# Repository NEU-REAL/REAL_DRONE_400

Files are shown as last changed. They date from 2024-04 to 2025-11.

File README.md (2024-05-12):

# **【东北大学REAL实验室】自主无人机组装教程** 

Github链接 [REAL_DRONE_400](https://github.com/NEU-REAL/REAL_DRONE_400/) An open source Drone Suite for Aerial Robot.

本文档是视频教程[【东北大学REAL实验室】自主无人机组装教学视频](https://www.bilibili.com/video/BV1hC411H7rh/)的配套文档

实验室主页 [东北大学REAL-LAB 环境感知与自主导航实验室](http://faculty.neu.edu.cn/fangzheng/zh_CN/zdylm/262140/list/index.htm)

  <div align=center>
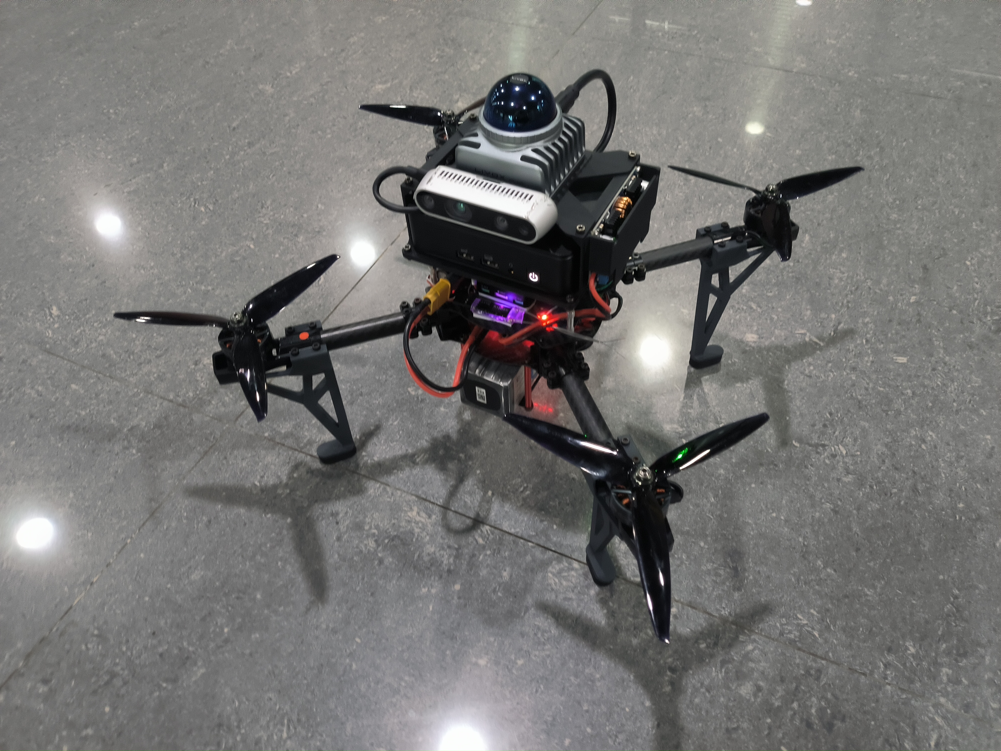
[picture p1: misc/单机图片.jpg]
  
  </div>

⭐项目亮点⭐

⭐结构件 动力套开源

⭐免雷达驱动一键编译

⭐输出高频雷达定位信息。

<font color="#dd0000">**教程简介**</font>

本次课程是一套面向对自主空中机器人感兴趣的学生、爱好者、相关从业人员的免费课程，包含了从硬件组装、代码部署、实机实验等全套详细流程。提供一种Fast-Drone-250的升级大负载能力、稳定定位版本自主无人机。本次课程所涉及的所有代码、硬件设计全部开源。<font color="#dd0000">严禁商用与转载，版权与最终解释权由东北大学REAL实验室所有。</font>

<font color="#dd0000">**安全事项**</font>

四旋翼无人机具有较高的安全风险，请同学们严格遵守安全规范，不要在有人的室内或室外进行试验，对自己和他人的安全负责，本实验室完全免责。

<font color="#dd0000">**致谢**</font>

感谢飞哥组里的小伙伴们提供的支持以及[FAST-DRONE-250开源项目](https://github.com/ZJU-FAST-Lab/Fast-Drone-250)以及[完整课程](https://www.shenlanxueyuan.com/course/385?source=1)。有兴趣的各位可以去点点⭐。

感谢组内指导老师方正教授的大力支持。

感谢一起调试、设计本构型无人机、提供了大力帮助的好伙伴孙哥和白哥。

# 教程视频链接：
- [第一节：无人机简介与电气连接](https://www.bilibili.com/video/BV1hC411H7rh/?vd_source=a901441d2c723973826f98ab4b1463a5)
- [第二节：工作台与焊接讲解](https://www.bilibili.com/video/BV1zC411H7ij/?vd_source=a901441d2c723973826f98ab4b1463a5)
- [第三节：无人机装配与飞控设置](https://www.bilibili.com/video/BV1Nx4y167wC/?vd_source=a901441d2c723973826f98ab4b1463a5)
- [第四节：PX4_Ctrl FSM讲解与真机定点飞行](https://www.bilibili.com/video/BV11i421y7ta/?vd_source=a901441d2c723973826f98ab4b1463a5)
- [第五节：Preception & Planning与真机飞行](https://www.bilibili.com/video/BV1G1421X7sd/?vd_source=a901441d2c723973826f98ab4b1463a5)

# 项目文件说明：
  项目中分为几个文件夹：
- [files](/files/) 文件夹用于存放各类相关文件
- [home_shfiles](/home_shfiles/) 存放了快速启动脚本，请将此目录下的脚本放置于home路径下以快速启动
- [misc](/misc/) 文件夹存放项目相关的图片资料
- [release](/release/) 文件夹存放项目的硬件设计资料，其中[3MF](/release/3MF/)文件夹存放需要打印的部件模型，我们使用拓竹X1C打印机进行3D打印部分材料制作，耗材使用拓竹PLA-CF。[PRODUCTION](/release/PRODUCTION/)文件夹存放可以直接打印的切片工程。[STEP](/release/STEP/)文件夹存放项目相关的所有硬件设计素材，以STEP文件给出。
- [src](/src/) 文件夹放置项目源码文件。

## 第一章：无人机简介与电气连接
  本次课程与高飞老师的[从零制作自主空中机器人](https://www.bilibili.com/video/BV1WZ4y167me?p=1)同样是一套面向对自主空中机器人感兴趣的学生、爱好者、相关从业人员的免费课程，包含了从硬件组装、机载电脑环境设置、代码部署、实机实验等全套详细流程，带你从0开始，组装属于自己的自主无人机，并让它可以在未知的环境中自由避障穿行。本次课程所涉及的所有代码、硬件设计全部开源，<font color="#dd0000">严禁商用与转载，版权与最终解释权由东北大学REAL实验室所有。</font>

  本次课程的重心主要落在自主空中机器人的搭建、代码部署及调试上，关于自主空中机器人的一些理论基础，例如动力学模型，路径搜索，轨迹规划，地图构建等内容，高飞老师在深蓝学院有非常详尽而深入浅出的[课程](https://www.shenlanxueyuan.com/course/385?source=1)，本次课程就不再赘述。

## 第二章：动力套焊接
  机器人本体相关配件及焊接用工具详见[purchase_list.xlsx](files/purchase_list.xlsx)

  **特别强调，四合一电调的输入电源线需要并联配套电解电容，且输入电源线规格至少应在14AWG以上，推荐12AWG与电池一致，保证过流能力！**

  焊接目标如图
  <div align=center>
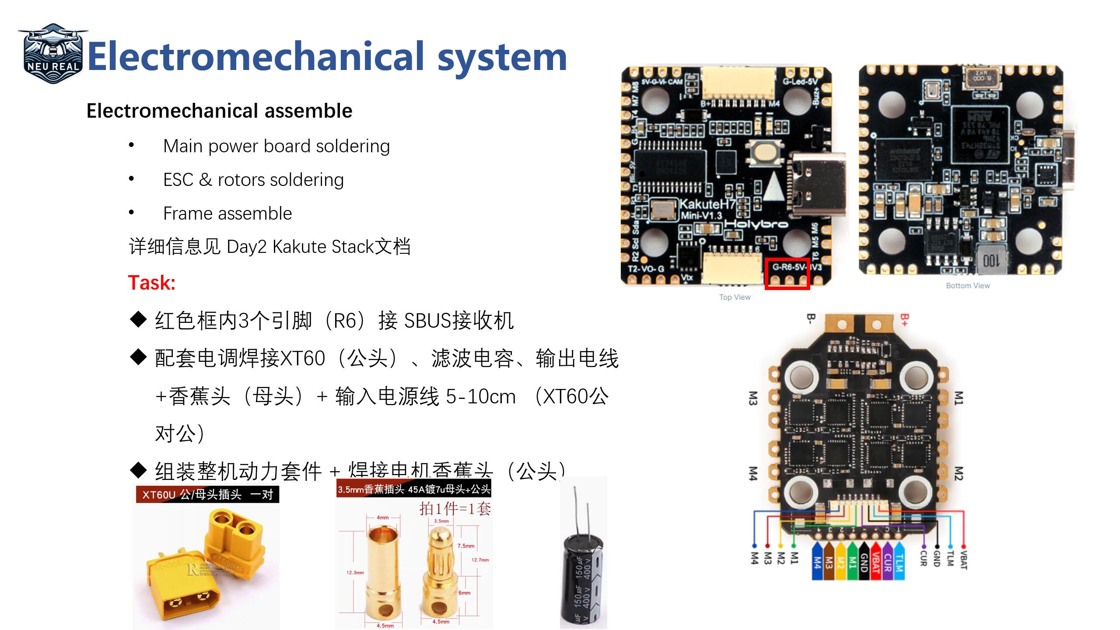
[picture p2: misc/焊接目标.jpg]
  
  </div>

  焊接最终结果如图
  <div align=center>
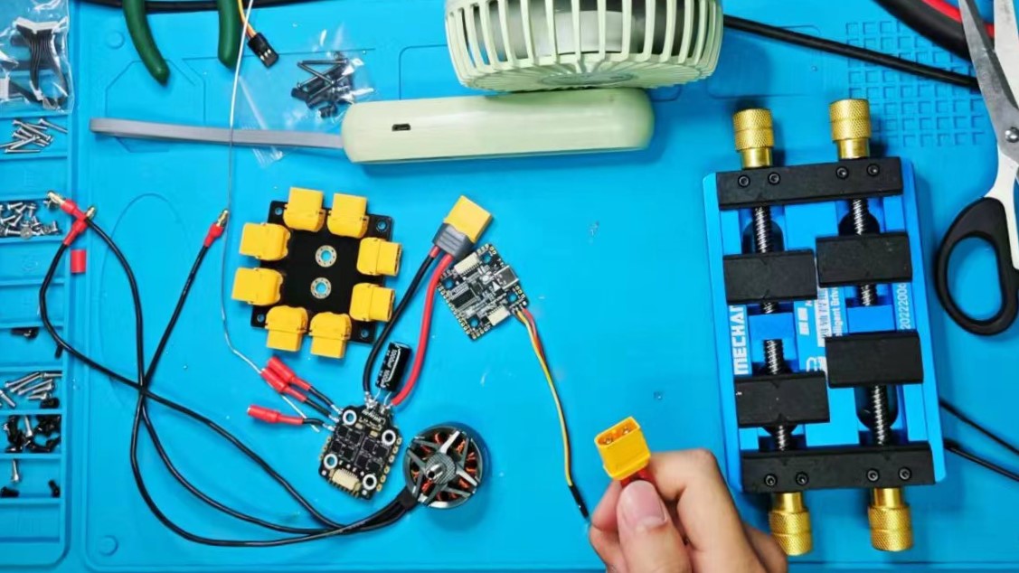
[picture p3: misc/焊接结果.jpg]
  
  </div>

## 第三章：无人机装配与飞控设置

使用QGC连接飞控，如果无法识别为PX4飞控，例如下图：
  <div align=center>
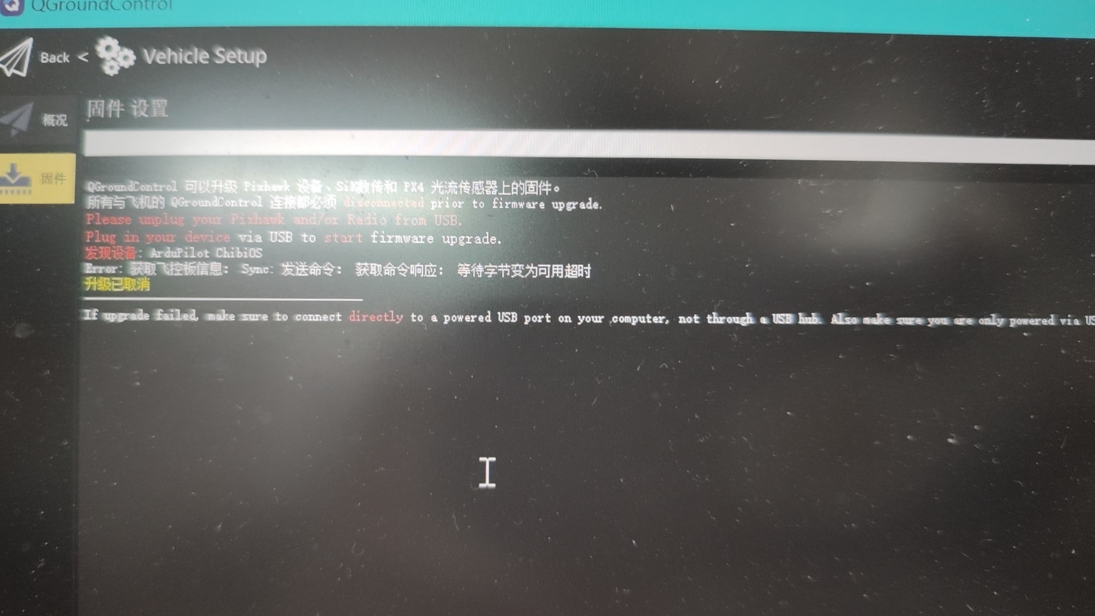
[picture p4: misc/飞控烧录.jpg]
  
  </div>

请按照以下步骤使用dfu-util 工具在ubuntu下刷飞控bootloader：

1.	长按飞控按钮同时插typec连接电脑，按里面txt的命令，在ubuntu下刷引导进去，注意路径
dfu-util -a 0 --dfuse-address 0x08000000 -D ./holybro_kakuteh7mini_bootloader/holybro_kakuteh7mini_bootloader.bin  

2.	进入qgc的固件界面，再重新插拔，自定义安装压缩包里的px4
再重新插拔应该就有了，这个操作可能会报error，不用管他。

    注意：刷1.14 beta版 
    stable版有bug会导致炸机 Dshot不是很稳定会导致怠速过快
    推荐用PWM400输出电调并调整死区至怠速解锁

* 上电前请先用万用表通断档检测电源正负焊点是否短接，强烈建议第一次上电前先接一个[短路保护器](https://item.taobao.com/item.htm?spm=a230r.1.14.6.72b83b20uNbZk7&id=656973651729&ns=1&abbucket=19#detail)

* <font color="#dd0000">检测电机转向前确保没有安装螺旋桨！！！！</font>

* 修改电机转向：调整转向错误电机的3根连接线中的其中两根交换相接即可。

## 第四章：PX4_Ctrl FSM讲解与真机定点飞行
- 自动起飞与定点控制
```
sh start_sensor.sh；
sh start_mapping.sh；
rostopic echo /Odom_high_freq；
```
拿起飞机进行缓慢的小范围晃动，放回原地后确认没有太大误差；
遥控器5通道拨到内侧，6通道拨到下侧，油门打到中位；
```
sh start_run_ctrl.sh；
sh start_takeoff.sh;
```
如果飞机螺旋桨开始旋转，但无法起飞，说明hover_percent参数过小；如果飞机有明显飞过1米高，再下降的样子，说明hover_percent参数过大；
遥控器此时可以以类似大疆飞机的操作逻辑对无人机进行位置控制；
```
sh start_land.sh
```
降落时把油门打到最低，等无人机降到地上后，把5通道拨到中间，左手杆打到左下角上锁。

## 第五章：Preception & Planning与真机飞行
  确认图中参数：
  <div align=center>
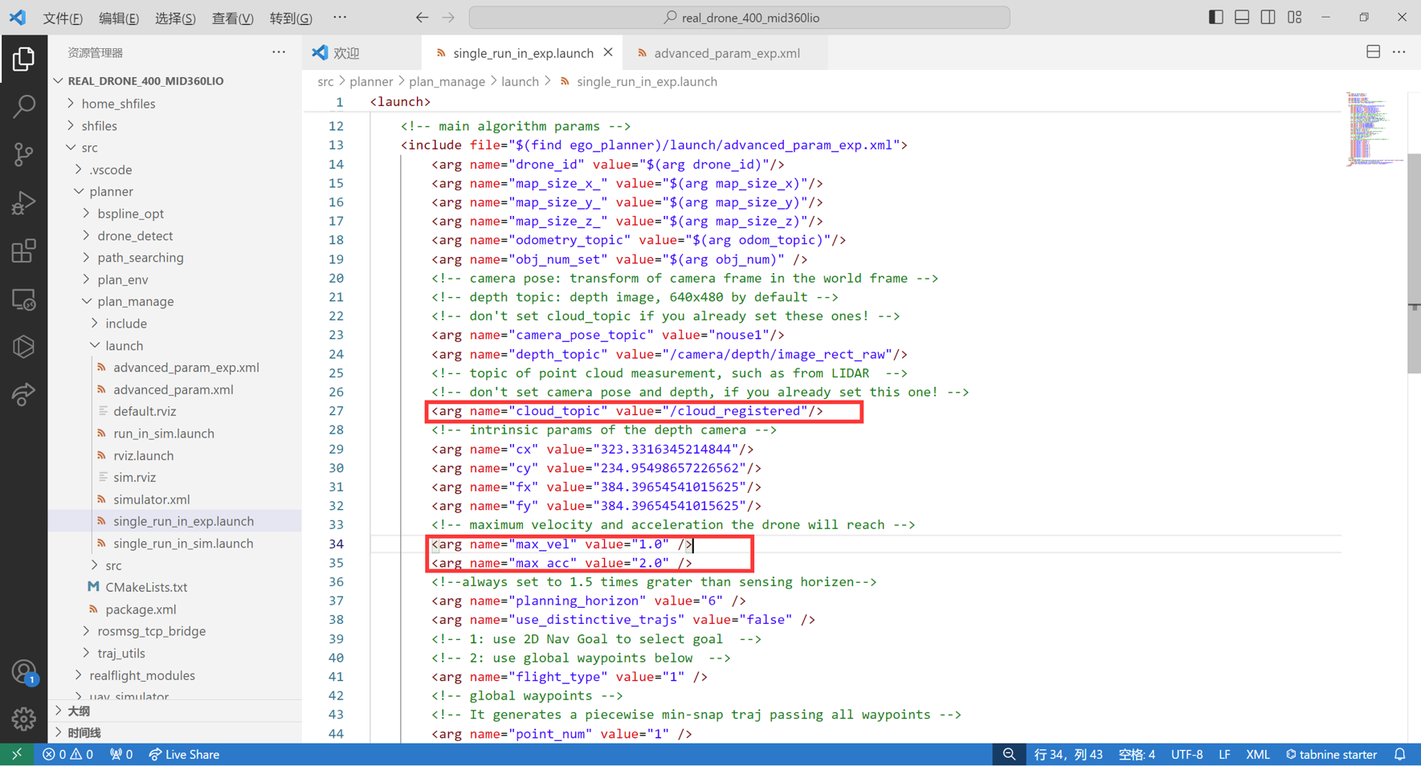
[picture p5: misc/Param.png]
  
  </div>

- Ego-Planner 真机测试

1.启动传感器与定位
```
sh start_sensor.sh；
sh start_mapping.sh；
rostopic echo /Odom_high_freq；
```
2.启动Ego-Planner与Rviz
```
sh start_planner.sh;
sh start_rviz.sh;
```
3.启动PX4_ctrl后确认摇杆正确，自动起飞
```
sh start_run_ctrl.sh；
sh start_takeoff.sh;
```
按下G键加鼠标左键点选目标点使无人机飞行。

4.任务完成后使用自动降落
```
sh start_land.sh；
```

# 合作与维护
我们会努力扩展所提出的系统并提高代码可靠性。持续维护这个项目

如有任何技术问题，请使用此项目的ISSUE功能。

如有商业咨询，请联系东北大学 方正 教授 (fangzheng@mail.neu.edu.cn)。

# 补充说明：
  如果你觉得这个项目对你能够有所帮助，可以点点⭐或者转发分享哦。
  
  附带几组3D设计图与实物图的对照：
  
  1.整机比对
  <div align=center>
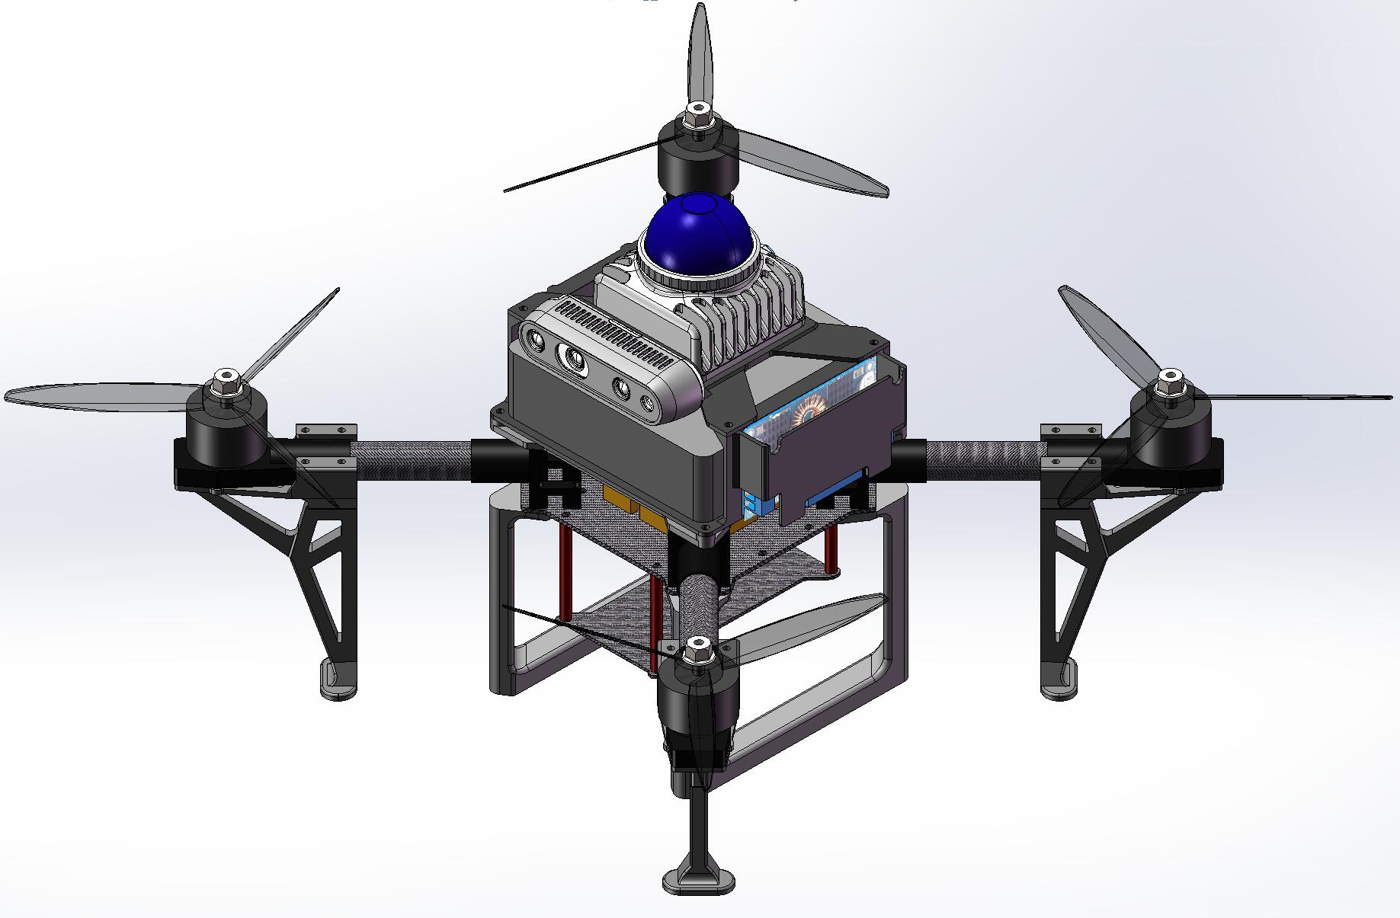
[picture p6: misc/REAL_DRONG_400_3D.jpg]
  
  </div>
  2.动力套件
  <div align=center>
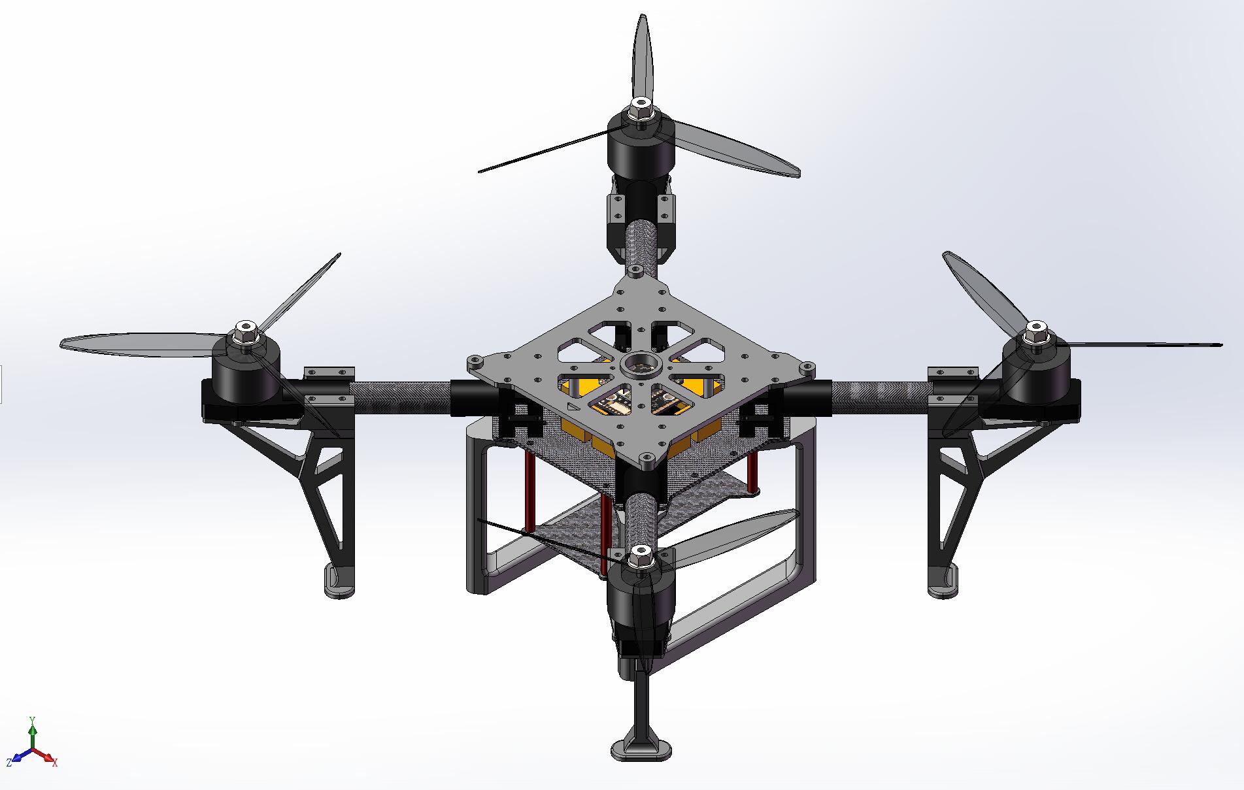
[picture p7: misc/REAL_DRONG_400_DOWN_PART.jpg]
  
  </div>
  3.感知模块
  <div align=center>
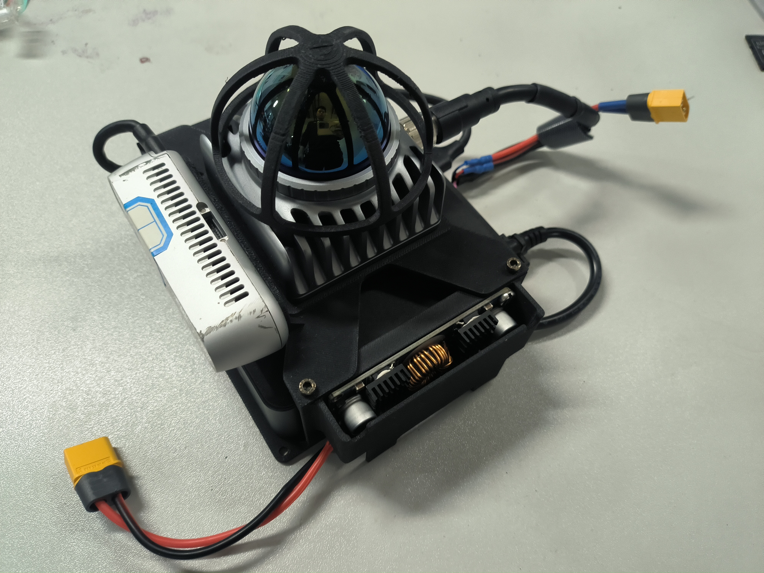
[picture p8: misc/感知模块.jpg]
  
  </div>

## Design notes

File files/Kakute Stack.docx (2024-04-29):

Kakute Mini H7 烧录教程 v1.1

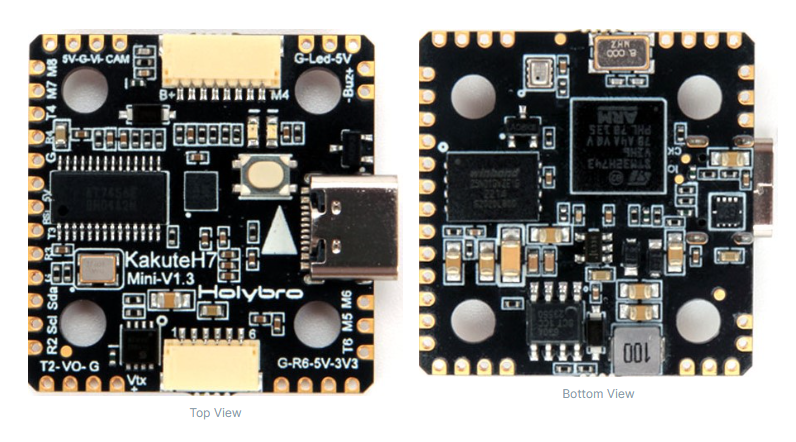
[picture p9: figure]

红色框内3个引脚（R6）接 SBUS接收机

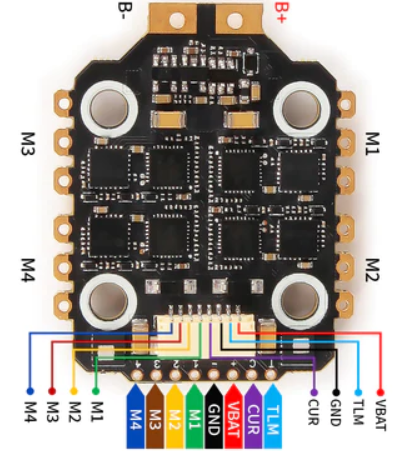
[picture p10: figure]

配套电调

1. 长按飞控按钮同时插typec连接电脑，按里面txt的命令，在ubuntu下刷引导进去，注意路径

dfu-util -a 0 --dfuse-address 0x08000000 -D ./holybro_kakuteh7mini_bootloader/holybro_kakuteh7mini_bootloader.bin

2. 进入qgc的固件界面，再重新插拔，自定义安装压缩包里的px4

再重新插拔应该就有了，这个操作可能会报error，不用管他。

注意：刷1.14 beta版

stable版有bug会导致炸机 Dshot不是很稳定会导致怠速过快

推荐用PWM400输出电调并调整死区至怠速解锁

PX4安装上就ok了，重新插拔可能会很慢连上，实在连不上就换Windows的qgc或者更新qgc试试

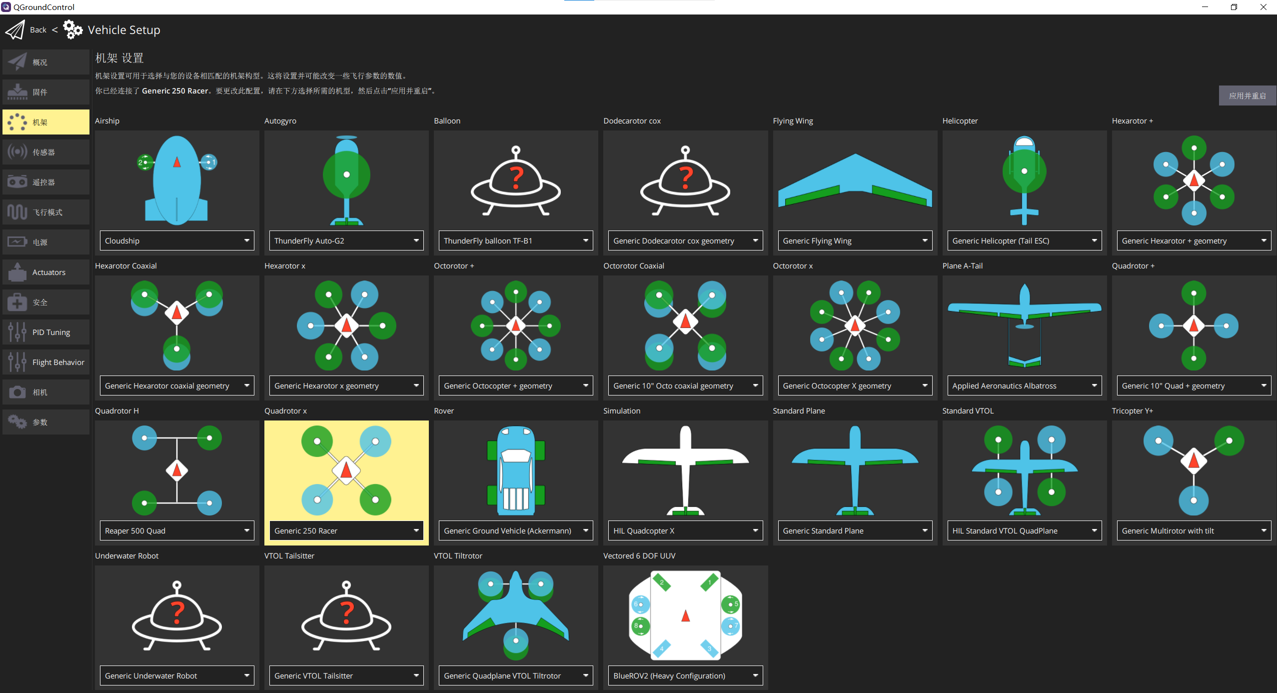
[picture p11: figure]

机架选择

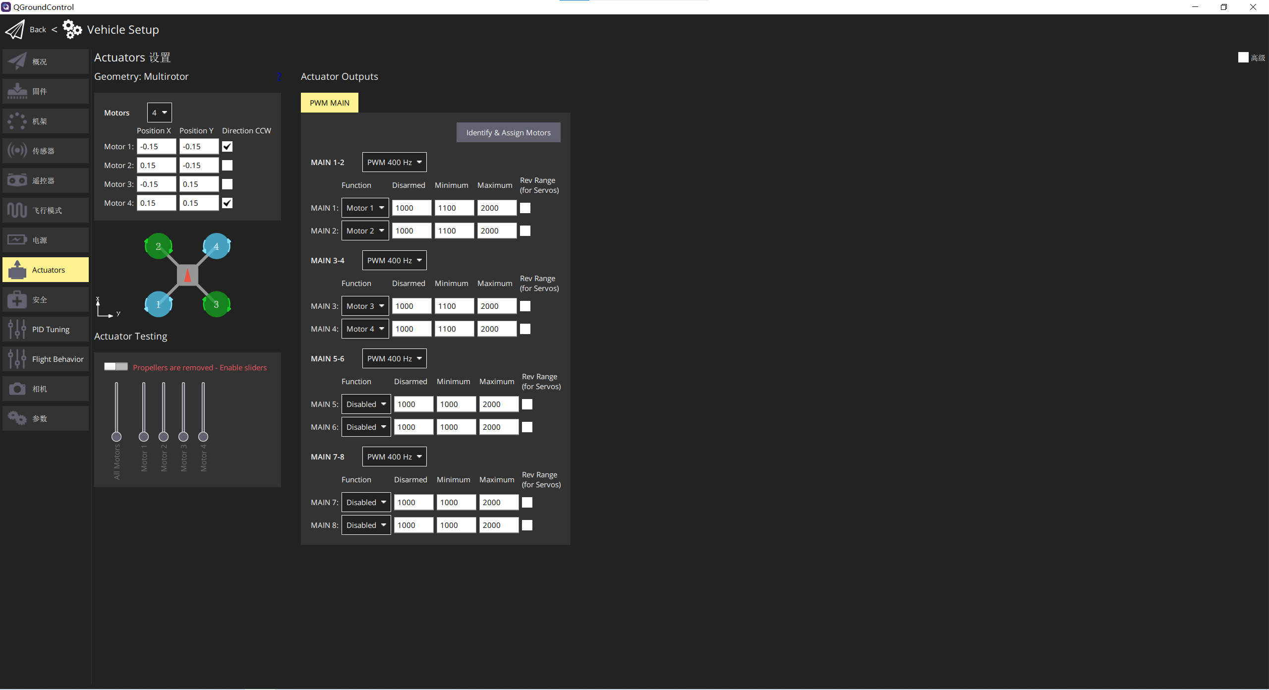
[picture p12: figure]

机架电机设置

©相关文档链接：

Kakute H7 Mini – Holybro Store (https://holybro.com/products/kakute-h7-mini)

Kakute H7 Mini Stacks – Holybro Store (https://holybro.com/products/kakute-h7-mini-stacks?variant=42940542746813)

Tekko32 F4 4in1 Mini 50A ESC – Holybro Store (https://holybro.com/products/tekko32-f4-4in1-mini-50a-esc?_pos=2&_psq=tekko32&_ss=e&_v=1.0)

Overview - Holybro Docs (https://docs.holybro.com/autopilot/kakute-h7-v1-v2-mini/kakute-h7-mini/overview)

Holybro Kakute H7 mini | PX4 自动驾驶用户指南 (main) (https://docs.px4.io/main/zh/flight_controller/kakuteh7mini.html)

PX4 Bootloader Flashing onto Betaflight Systems | PX4 自动驾驶用户指南 (main) (https://docs.px4.io/main/zh/advanced_config/bootloader_update_from_betaflight.html)

Update 2023.12.10 By Kangkang

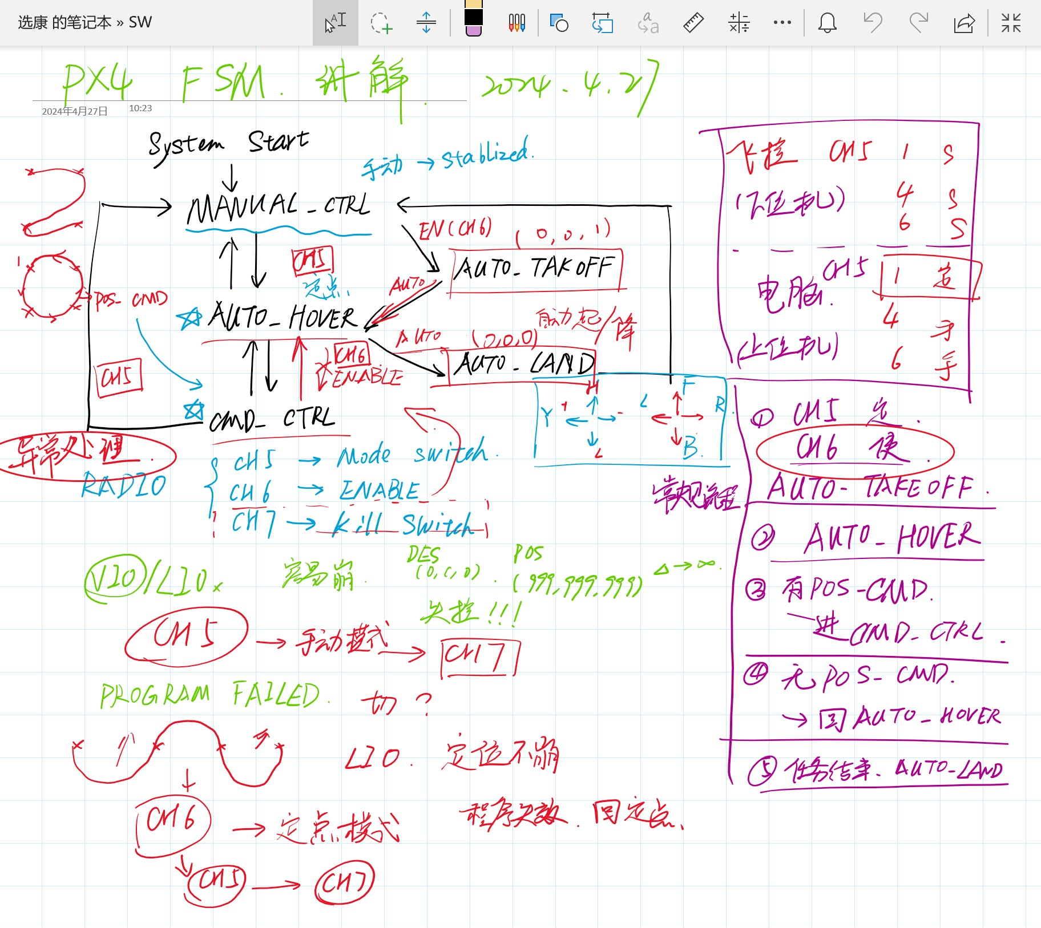
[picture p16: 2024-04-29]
misc/Handwriting.png

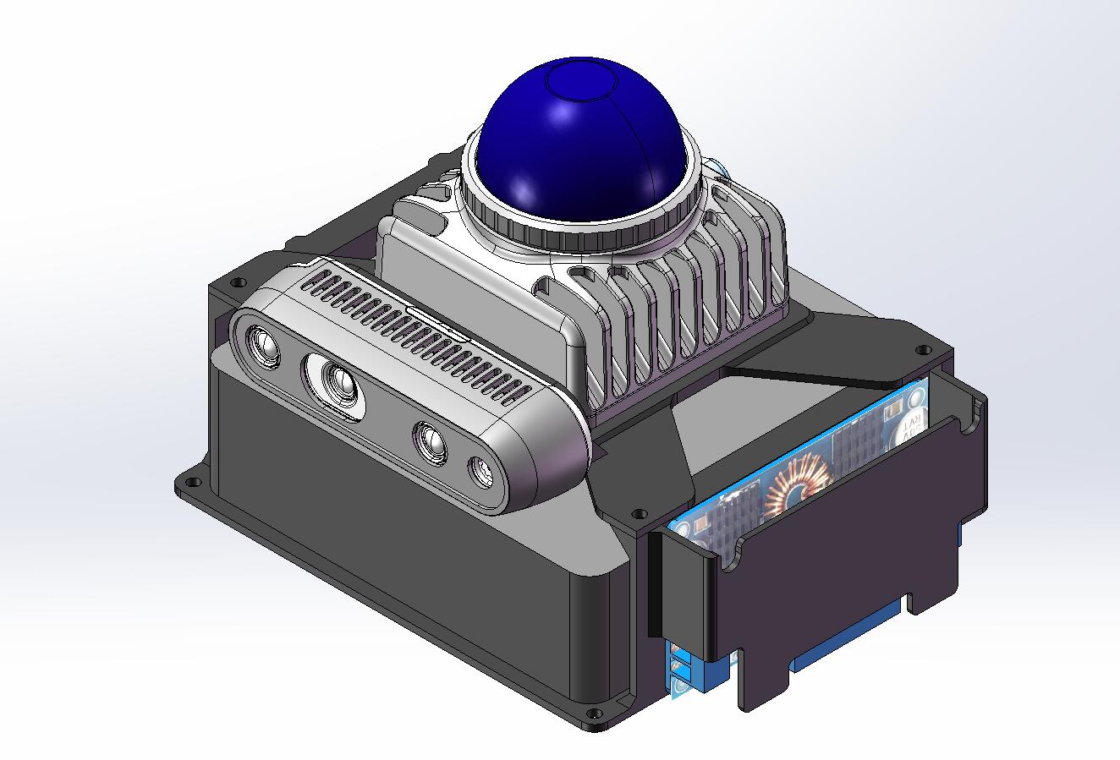
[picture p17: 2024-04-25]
misc/REAL_DRONG_400_UPPER_PART.jpg

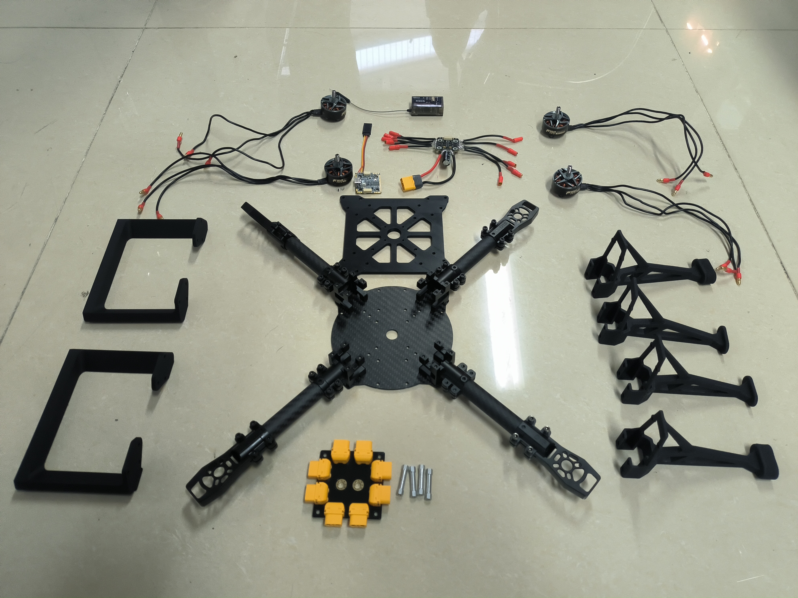
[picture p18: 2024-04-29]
misc/零件图.jpg

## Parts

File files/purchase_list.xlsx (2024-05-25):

类目 | 型号 | 数量 | 单价 | 总价 | 购买链接
动力套装
机架 | LJI-X400 Pro | 1 | 288 | 288 | https://item.taobao.com/item.htm?_u=d3ovgp2s356d&id=661322510447&sku_properties=31309:16741168228
无刷电机 | T-Motor F100 KV1100 | 4 | 229 | 916 | https://item.taobao.com/item.htm?_u=d3ovgp2s37a9&id=666218265469&sku_properties=31309:18046510136
飞控+电调 | H7 MINI + F4 4IN1 MINI 50A ESC | 1 | 916 | 916 | https://item.taobao.com/item.htm?_u=d3ovgp2s075e&id=695089334583&skuId=4934678877288
桨叶 | HQ 7040-3 | 1 | 15 | 15 | https://item.taobao.com/item.htm?_u=t3ovgp2s460a&id=671633881954&skuId=5010241515719
接收机 | 乐迪 R12DSM | 1 | 93 | 93 | https://item.taobao.com/item.htm?spm=a1z09.2.0.0.2abd2e8da0sHzh&id=541658831753&_u=l32egecq5116
遥控器 | 乐迪 AT9S PRO 左手不回中 | 1 | 545 | 545 | https://item.taobao.com/item.htm?_u=t3ovgp2s8571&id=620560690486&skuId=4648673175694
电池 | 格氏 4000mAh 6S | 1 | 488 | 488 | https://detail.tmall.com/item.htm?_u=t3ovgp2sa7dc&id=14832015119&spm=a1z09.2.0.0.32aa2e8df64WUL
穿越机脚垫 | 30*15*10mm | 1 | 16.99 | 16.99 | https://item.taobao.com/item.htm?_u=t3ovgp2se7b0&id=562158533089&skuId=3961675618573
 |  |  | 动力套成本 | 3277.99
感知模块配件
DC供电线 | XT60 | 1 | 13 | 13 | https://item.taobao.com/item.htm?spm=a1z09.2.0.0.773d2e8despLGo&id=613472402389&_u=g2epqo5e38f7
飞控连接线 | 双左弯0.15m | 1 | 9.5 | 9.5 | https://detail.tmall.com/item.htm?id=43144333772&_u=i32egecqf5d3&skuId=4498792030458
TYPEC连接线 | 15cm | 1 | 22.9 | 22.9 | https://detail.tmall.com/item.htm?id=617461584216&spm=a1z09.2.0.0.2abd2e8da0sHzh&_u=l32egecq0e19
HDMI欺骗器 |  | 1 | 3 | 3 | https://item.taobao.com/item.htm?id=600829968368&ali_trackid=1_b8192277632fc8796a134ac616741b67
DC-DC稳压模块 | LTC3780 | 1 | 38 | 38 | https://item.taobao.com/item.htm?_u=p3ovgp2s988d&id=537511849240&spm=a1z09.2.0.0.19c62e8dwykGML
 |  |  | 感知模块配件成本 | 48.4
感知模块核心
机载电脑 | Intel NUC 猛虎峡谷 准系统 i5 薄款 | 1 | 2590 | 2590 | https://item.taobao.com/item.htm?id=638758423001&ns=1&abbucket=3
 | 三星 DDR4内存条 8G 3200hz | 1 | 229 | 229 | https://detail.tmall.com/item.htm?id=541378489978&spm=a1z09.2.0.0.ea4d2e8dwctqDn&_u=t2epqo5eaa9f
 | 影驰黑将 250G M.2固态硬盘 | 1 | 234 | 234 | https://detail.tmall.com/item.htm?id=541378489978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
双目深度相机 | INTEL REALSENSE D435 | 1 | 2180 | 2180 | https://item.taobao.com/item.htm?spm=a1z10.1-c.w4004-8474743471.36.1f164e1fL0mvDM&id=670494420704
激光雷达 | Livox Mid-360 | 1 | 3999 | 3999 | https://store.dji.com/cn/product/livox-mid-360?vid=130851
 |  |  | 感知模块核心成本 | 9232
3D打印零件
上板 | 上板 | 1 | Nan | Nan
脚架 | 脚架 | 1 | Nan | Nan
感知模块支架 | 感知模块支架 | 1 | Nan | Nan
 |  |  | 3D打印成本 | Nan
配件
硅胶线 | 20,18,16AWG | 若干 | Nan | Nan | https://item.taobao.com/item.htm?id=631990884181&ns=1&abbucket=3
BB响 |  | 1 | Nan | Nan | https://item.taobao.com/item.htm?id=13954041762&ns=1&abbucket=3
硅胶杜邦线 | 10cm,15cm，公对母 | 若干 | Nan | Nan | https://item.taobao.com/item.htm?id=567943637652&ali_trackid=1_82cb0cae98e77d6ab8f389660ffac1cf
3.5mm香蕉头 公母头 |  | 12 | Nan | Nan
XT60公、母头 |  | 1 | Nan | Nan
双通铝柱 | M3*25 | 4 | Nan | Nan | https://item.taobao.com/item.htm?id=603331087035&ns=1&abbucket=13
3M双面胶 | 20mm*3m | 1 | Nan | Nan | https://detail.tmall.com/item.htm?id=653733592411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
螺丝 | M3*6mm M3*8mm 杯头 | 若干 | Nan | Nan | https://detail.tmall.com/item.htm?id=624811454452&_u=i32egecq19dc&skuId=4601948603338
 |  |  | 配件成本 | Nan
工具
烙铁 | AT937标配 | 143 | 1 | 143 | https://item.taobao.com/item.htm?id=7800035658&ns=1&abbucket=14
烙铁头 | 900M-1.6K | 11 | 1 | 11 | https://item.taobao.com/item.htm?spm=a1z10.3-c-s.w4002-23344838098.27.754f1004qeCAY6&id=579728085148
海绵 |  | 2 | 1 | 2 | https://item.taobao.com/item.htm?spm=a1z10.3-c-s.w4002-23344838098.9.6d6c1004U43LPK&id=7586598250
焊锡 | 0.5mm 500g | 76.67 | 1 | 76.67 | https://detail.tmall.com/item.htm?spm=a230r.1.14.11.552520bejLfPiP&id=43741015860&ns=1&abbucket=14
夹持台 | 褐色 | 75 | 1 | 75 | https://item.taobao.com/item.htm?id=613902998667&ali_trackid=1_a8d9bfa88456e4bdeb5141959028dacf
扳手 |  | 11 | 1 | 11 | https://item.taobao.com/item.htm?id=610029436080&ns=1&abbucket=14
螺丝刀 | 2.0mm、2.5mm | 10.99 | 1 | 10.99 | https://detail.tmall.com/item.htm?id=572329178882&cm_id=140105335569ed55e27b&abbucket=14
万用表 |  | 49 | 1 | 49 | https://item.jd.com/100000287597.html
剪刀 | 3把中号 | 10.9 | 0.33 | 3.597 | https://item.jd.com/6020791.html
切割垫 | A3 | 19.9 | 1 | 19.9 | https://item.jd.com/100001317628.html
 |  |  | 工具成本 | 402.157

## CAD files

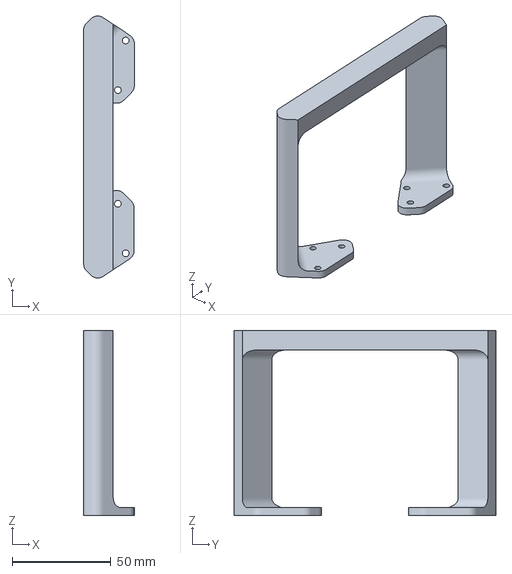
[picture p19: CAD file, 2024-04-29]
release/3MF/horrizon_land_support.3MF
25.8 x 133.0 x 94.0 mm

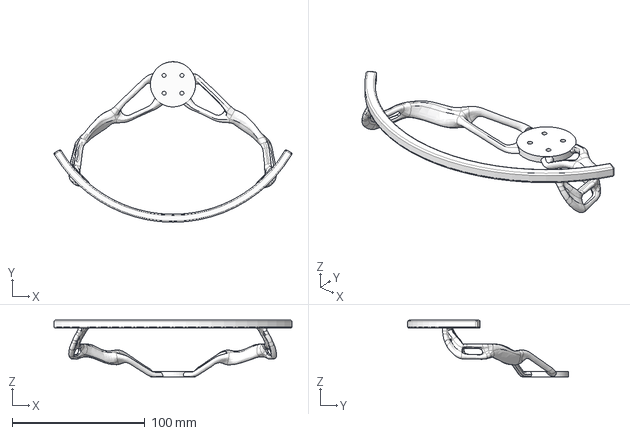
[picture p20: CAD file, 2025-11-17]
release/Derivative Design/R7040_GD_0525_001_Result_001.step
179.1 x 120.8 x 42.6 mm

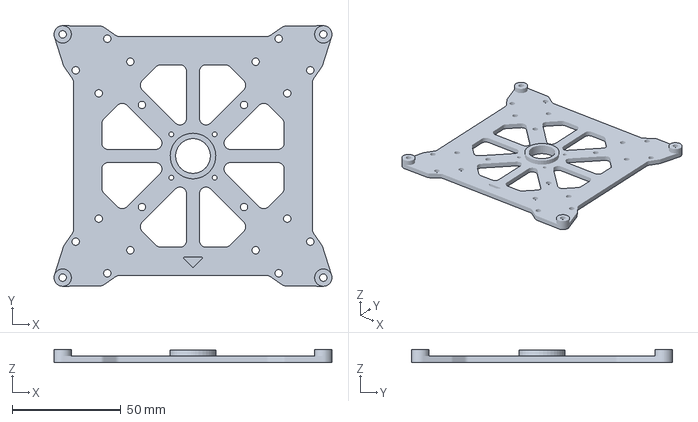
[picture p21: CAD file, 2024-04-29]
release/PRODUCTION/机架上板.3mf
128.0 x 120.0 x 6.00 mm

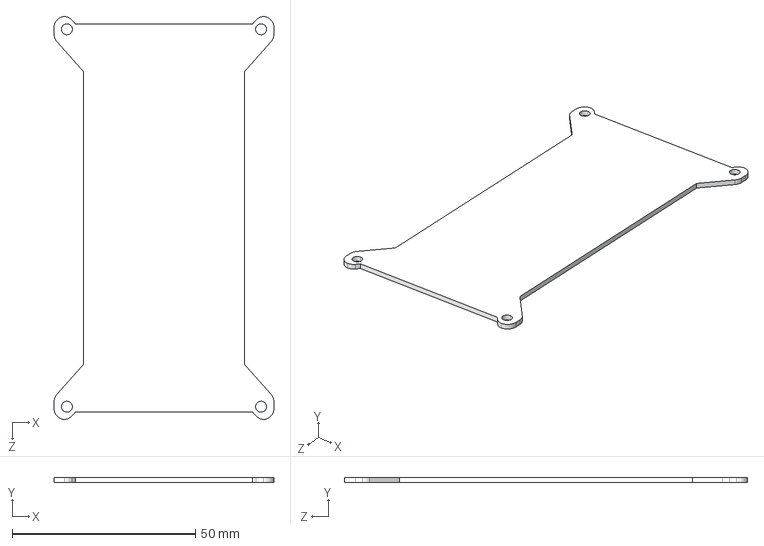
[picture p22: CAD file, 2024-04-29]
release/STEP/电池仓板.STEP
60.0 x 1.50 x 110.0 mm

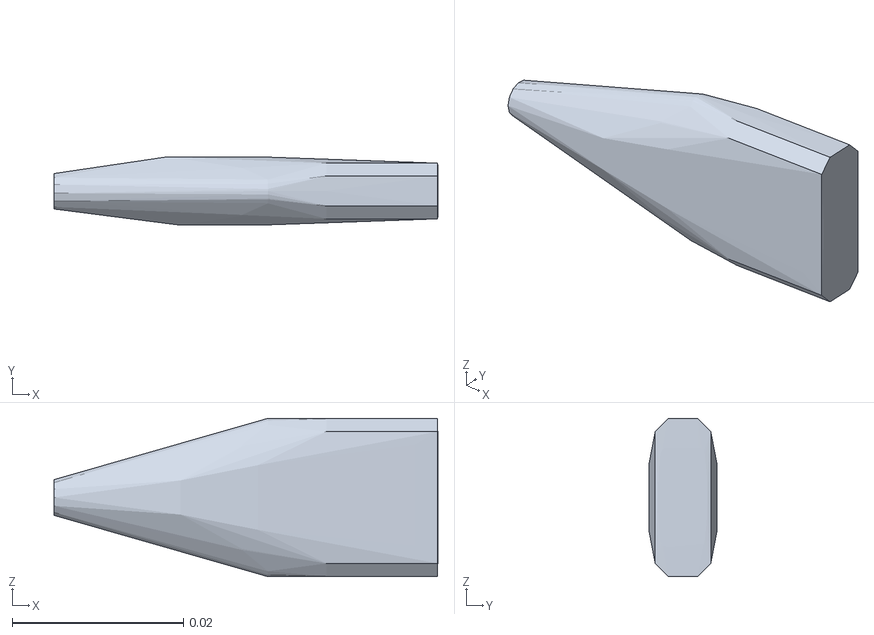
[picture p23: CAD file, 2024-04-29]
src/realflight_modules/realsense-ros/realsense2_description/meshes/plug_collision.stl
0.0448 x 0.008 x 0.0185

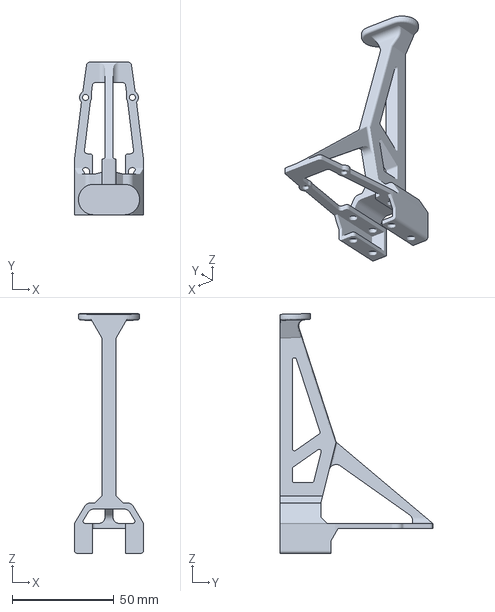
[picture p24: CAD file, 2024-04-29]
release/3MF/new-land-support.3MF
34.0 x 75.0 x 118.0 mm

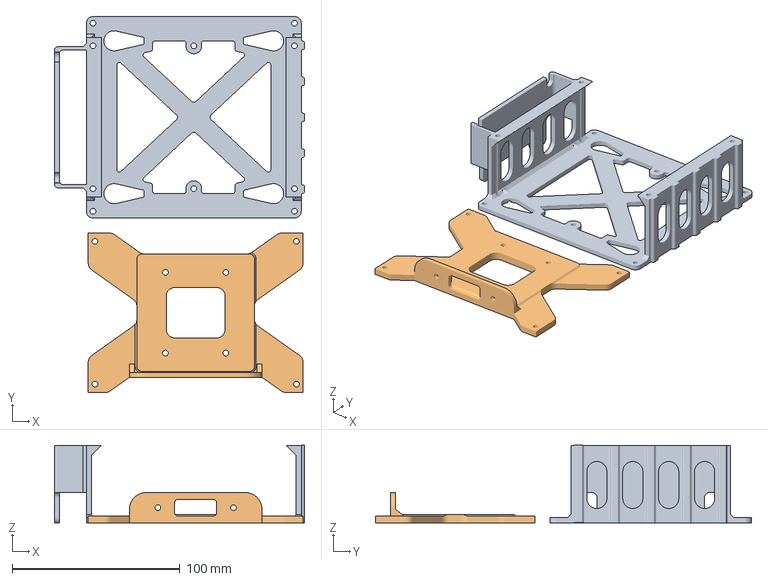
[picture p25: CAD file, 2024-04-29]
release/PRODUCTION/感知模组.3mf
149.0 x 223.9 x 46.2 mm
nuc-board-加厚
mid360-realsense-board-加厚

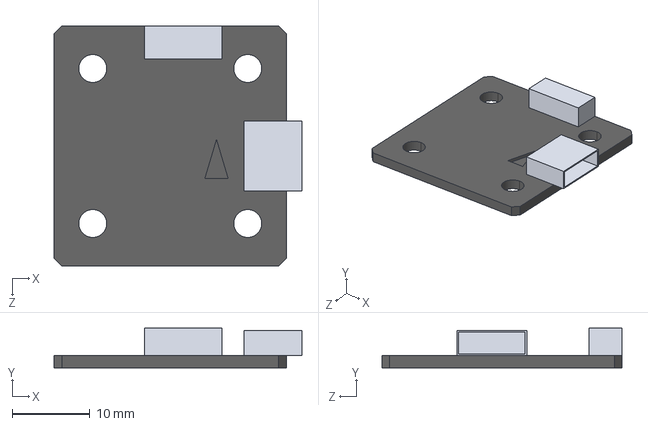
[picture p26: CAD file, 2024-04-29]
release/STEP/kakute_H7_mini.STEP
32.0 x 5.10 x 31.0 mm

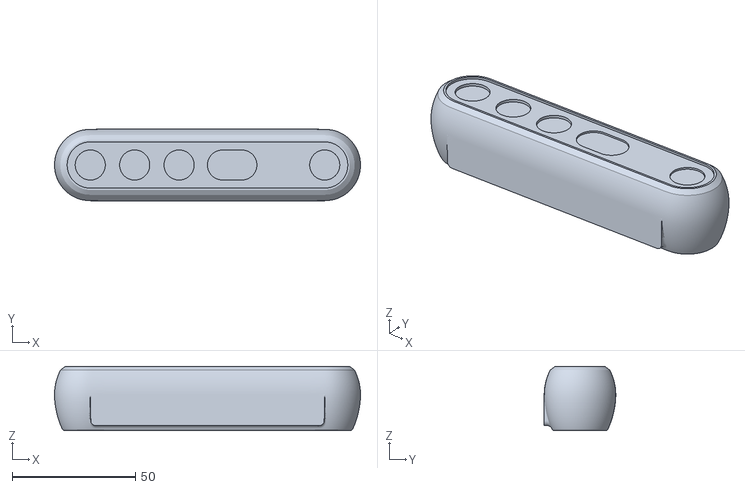
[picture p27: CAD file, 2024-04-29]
src/realflight_modules/realsense-ros/realsense2_description/meshes/d455.stl
124.0 x 29.0 x 26.0

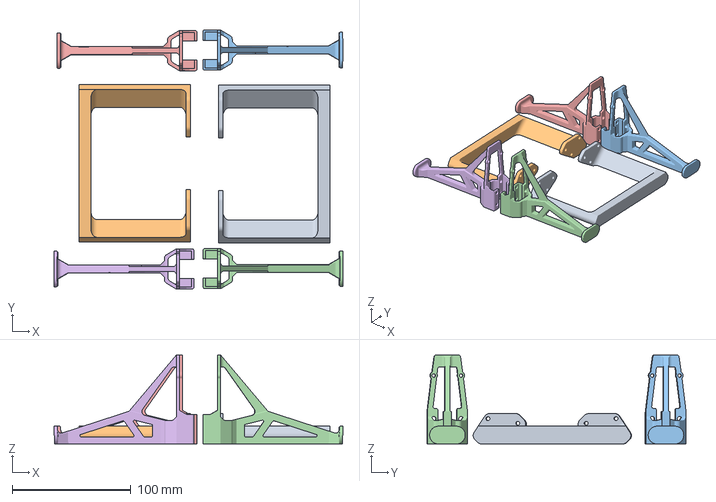
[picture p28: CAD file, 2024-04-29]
release/PRODUCTION/全套脚架.3mf
243.7 x 218.7 x 75.0 mm
水平脚架 x 2
new-land-support x 4

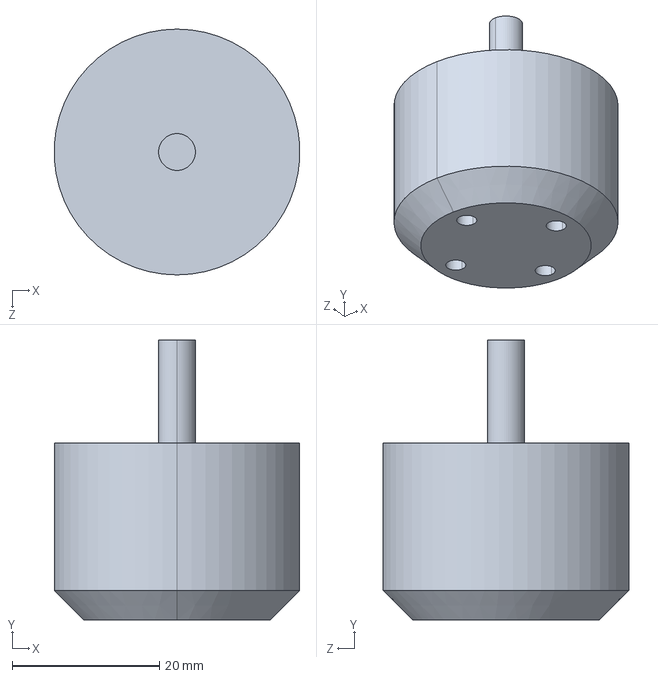
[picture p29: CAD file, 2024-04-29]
release/STEP/F100-m2810.STEP
33.3 x 38.0 x 33.4 mm

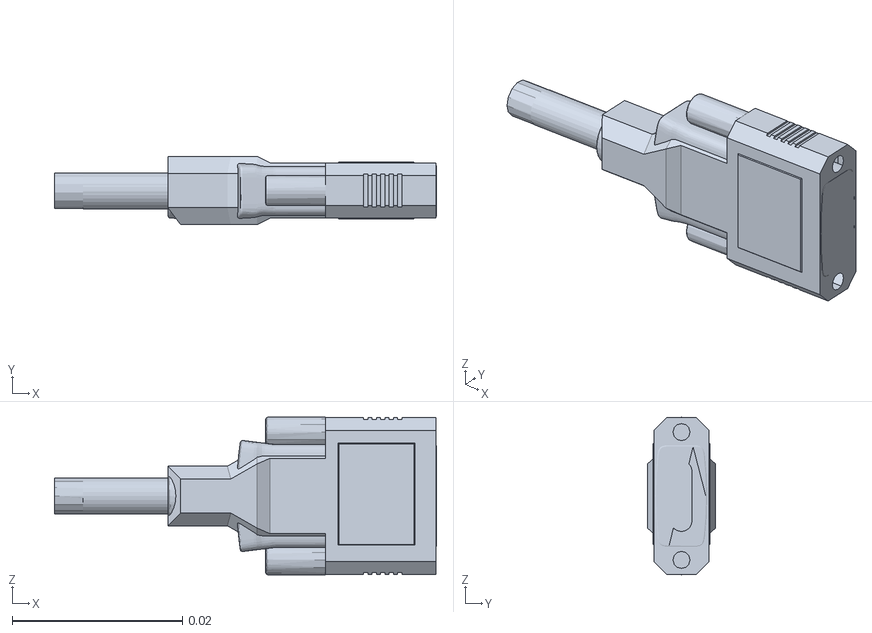
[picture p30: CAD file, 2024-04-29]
src/realflight_modules/realsense-ros/realsense2_description/meshes/plug.stl
0.0448 x 0.008 x 0.0185

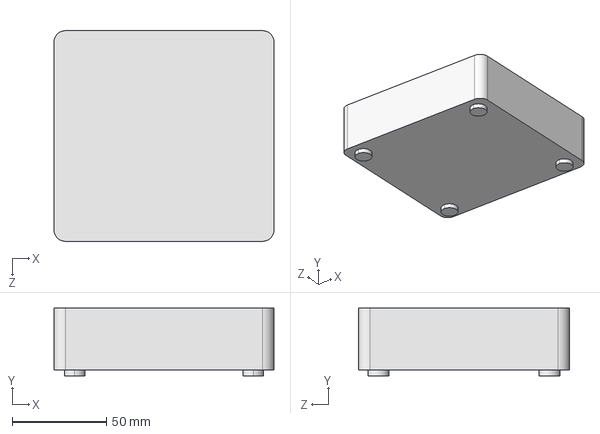
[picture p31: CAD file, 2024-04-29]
release/STEP/nuc.STEP
117.0 x 36.0 x 112.0 mm

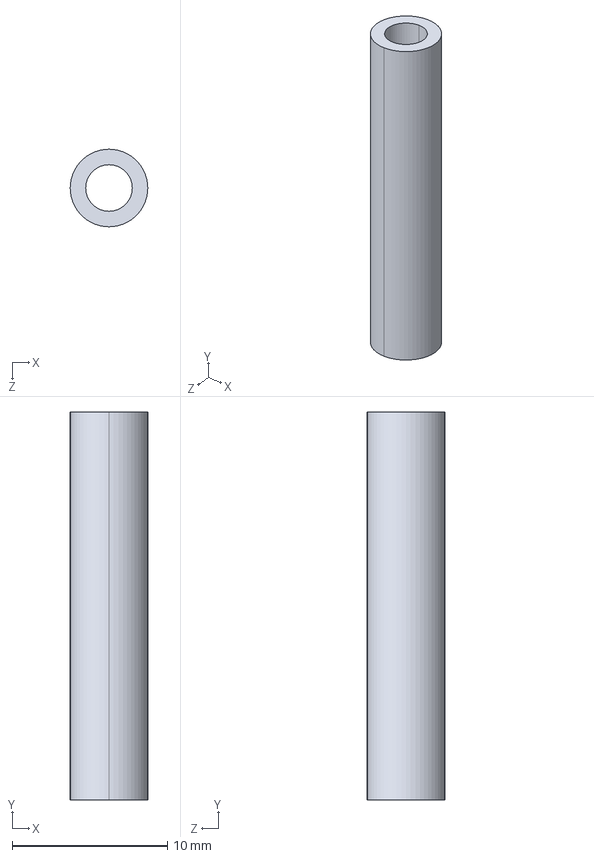
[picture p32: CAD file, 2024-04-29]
release/STEP/25mm铝柱-分电板.STEP
5.00 x 25.0 x 5.00 mm

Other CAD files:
release/STEP/mid360-realsense-board.STEP
release/STEP/50mm铝柱-电池仓.STEP
release/STEP/分电板.STEP
release/STEP/upper-board.STEP
release/3MF/bottom-board.3MF
release/3MF/mid360-realsense-board.3MF
release/3MF/nuc-board.3MF
release/3MF/upper-board.3MF
release/STEP/HQ7040×3-ccw.STEP
release/STEP/HQ7040×3-cw.STEP
release/STEP/LTC3780.STEP
release/STEP/bottom-board.STEP
release/STEP/carbon_tube.STEP
release/STEP/land-support.STEP
release/STEP/motor-hold.STEP
release/STEP/nuc-board.STEP
release/STEP/tekko32.STEP
release/STEP/机臂连接.STEP
release/STEP/水平脚架.STEP

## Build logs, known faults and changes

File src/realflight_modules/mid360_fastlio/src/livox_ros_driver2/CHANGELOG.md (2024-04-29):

# Changelog

All notable changes to this project will be documented in this file.

## [1.2.3]
### Fixed
- Optimize framing logic and reduce CPU usage
- Fixed some known issues

## [1.2.1]
### Fixed
- Fix offset time error regarding CustomMsg format message publishment.

## [1.2.0]
### Added
- Revise the frame segmentation logic.
- (Notice!!!) Add Timestamp to each point in Livox pointcloud2 (PointXYZRTLT) format. The PointXYZRTL format has been updated to PointXYZRTLT format. Compatibility needs to be considered.
### Fixed
- Improve support for gPTP and GPS synchronizations.

--- 
## [1.1.3]
### Fixed
- Improve performance when running in ROS2 Humble.

--- 
## [1.1.2]
### Changed
- Change publish frequency range to [0.5Hz, 10 Hz].
### Fixed
- Fix a high CPU-usage problem.

--- 
## [1.1.1]
### Added
- Offer valid line-number info in the point cloud data of MID-360 Lidar.
- Enable IMU by default.
### Changed
- Update the README slightly.

--- 
## [1.0.0]
### Added
- Support Mid-360 Lidar.
- Support for Ubuntu 22.04 ROS2 humble.
- Support multi-topic fuction, the suffix of the topic name corresponds to the ip address of each Lidar. 
### Changed
- Remove the embedded SDK.
- Constraint: Livox ROS Driver 2 for ROS2 does not support message passing with PCL native data types.
### Fixed
- Fix IMU packet loss.
- Fix some conflicts with livox ros driver.
- Fixed HAP Lidar publishing PointCloud2 and CustomMsg format point clouds with no line number.

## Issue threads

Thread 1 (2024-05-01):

关于校准的问题

zbcUN, 2024-05-01:
您好 非常感谢您的工作，他对我非常有帮助。但是我的雷达和相机安装位置与您的不同，需要注意哪些校准问题吗？ 此外我看到视频里egoplaner的避障用到的像是激光雷达。在这个项目里面realsense是否有用到？

TheConquerK, 2024-05-06:
你好，感谢你的对项目的肯定。在这个问题中，校准即外参标定是肯定需要的，我们现在的坐标系是以雷达的IMU为Body系建立的，和飞控IMU以及Realsense立体相机均存在一个静态的TF变换，这个变换矩阵可以通过我们提供的STEP模型直接计算，或者我们推荐使用Kalibr框架进行精确的外参标定，精确的外参会在项目的后续更新中给出。

Closed 2024-05-06.

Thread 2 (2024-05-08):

轨迹跟踪效果比较差

zbcUN, 2024-05-08:
我的飞机是用的450机架，是这个算法，超调现象有点严重，经常会撞到周围物体。请问您有什么建议吗？

TheConquerK, 2024-05-08:
450机架的配套动力套机动性是比较差的，px4_ctrl的PID参数需要重新整定。

TheConquerK, 2024-05-08:
450机架的配套动力套机动性是比较差的，px4_ctrl的PID参数需要重新整定。
可以尝试如下步骤：
1. 飞机定点模式起飞
2. 调整 src/realflight_modules/px4ctrl/config/ctrl_param_fpv.yaml 中的
三轴PD参数
 gain:
    # Cascade PID controller. Recommend to read the code.
    Kp0: 2.0
    Kp1: 2.0
    Kp2: 2.0
    Kv0: 1.5
    Kv1: 1.5
    Kv2: 1.5
3.在飞行模式下微调后载入
rospram load ctrl_param_fpv.yaml
4.使用遥控器改变悬停点查看控制器效果，使用QGC观察控制效果，输出为目标点与实际位置曲线

注意：这种调试方法有一定风险，需要有熟练的飞手救机，在载入参数之前确保修改参数不会过大，且相对合理

TheConquerK, 2024-05-08:
如果有效果可以给我反馈，之后我会关闭这个问题

zbcUN, 2024-05-11:
好的等我飞机修好后调试给您反馈，
我还有一个问题想请教，我们电机用的2250kv的tmotorf60.我们的飞机有2.5kg重。电池是5200mah。续航时间非常短。是电机的问题吗？换成您项目里kv1100点tmotor是否会有改进？

TheConquerK, 2024-05-11:
无人机太重了，动力套负载不太够，建议更换

zbcUN, 2024-05-15:
您好 我的无人机修好了  我尝试了定点模式，前后左右飞在速度不快的情况下还算稳 但是上下很不稳  上下会一直震荡，您有什么建议吗，现在您发的那些值改成了  3 3 3 2 2 2

zbcUN, 2024-05-22:
谢谢您的建议。我拆掉了深度相机。拆掉了电脑的外壳 现在整机算电池重量在1.89kg。根据淘宝上的参数我的四个电机应该有6104g推力。可是在起飞后的悬停阶段还是会上下震荡。但是在cmd模式不会抖动。也就是给定目标点后飞机z轴不会震荡。着有可能是什么原因呢？您是否有碰到过类似情况。

TheConquerK, 2024-05-24:
尝试调整z轴参数应该能够解决，之前我有遇到过，不过基本上就是参数的问题。

zbcUN, 2024-05-29:
您好，我参数还是调的毫无头绪，貌似它很难调，我又尝试开启了精准推力控制，在某些情况下是可以稳定的 但也有很多时候会突然无法起飞，例如电池刚刚冲满电时。
  同时我看见px4ctrl里面有一个精准推力控制校准的软件，但我没想明白它是如何使用。

Closed 2024-05-08.

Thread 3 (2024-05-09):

Reject AUTO_TAKEOFF

ranjithlesoko, 2024-05-09:
[ INFO] [1709288461.395479347]: PX4CTRL] Waiting for RC
[ INFO] [1709288461.402635812]: [PX4CTRL] RC received.
[ INFO] [1709288462.613087580]: [px4ctrl] Voltage=4.826, percentage=1.000
[ERROR] [1709288468.683143015]: [px4ctrl] Reject AUTO_TAKEOFF. If you have your RC connected, keep its switches at "auto hover" and "command control" states, and all sticks at the center, then takeoff again.
if i remove rc_data.is_hover_mode  in line 100 it arm and  takeoff
 i am using herelink how to set hover_mode to true

if ( !rc_data.is_command_mode || !rc_data.check_centered())
				{
					ROS_ERROR("[px4ctrl] Reject AUTO_TAKEOFF. If you have your RC connected, keep its switches at \"auto hover\" and \"command control\" states, and all sticks at the center, then takeoff again. is_hover_mode: %d, is_command_mode: %d, sticks_centered: %d", rc_data.is_hover_mode, rc_data.is_command_mode, rc_data.check_centered());

					while (ros::ok())
					{
						ros::Duration(0.01).sleep();
						ros::spinOnce();
						if (rc_data.is_hover_mode && rc_data.is_command_mode && rc_data.check_centered())
						{
							ROS_INFO("\033[32m[px4ctrl] OK, you can takeoff again.\033[32m");
							break;
						}
					}
					break;
				}

TheConquerK, 2024-05-10:
Channel 6 is an enabled channel, with only two numerical values to distinguish. You can print out the assigned BOOL amount in the program to view it. Make sure that channel 6 enables the drone to take off automatically during automatic takeoff. If not, the error you are experiencing now will appear.

ranjithlesoko, 2024-05-10:
@TheConquerK  if  i give this if ( !rc_data.is_command_mode || !rc_data.check_centered()) it get take off  i remove ! is_hover_mode  @TheConquerK  i cant find the logic  Channel 6   in  code

TheConquerK, 2024-05-10:
You can check src/realflight_modules/px4ctrl/src/input.cpp AND find where channel 6 is used in this Program. Changing code is not recommanded.

ranjithlesoko, 2024-05-13:
@TheConquerK  thanks

ranjithlesoko, 2024-05-14:
issue fixed thanks @TheConquerK

TheConquerK, 2024-05-14:
Okay. @ranjithlesoko

Closed 2024-05-10.

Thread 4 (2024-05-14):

关于增加T265

zouqingxiao, 2024-05-14:
首先，非常感谢课题组开源资料助力国内自主无人机发展。有两个小问题请教：
1. 我计划拿掉激光雷达，换成T265做室内定位输出odom，这样就不用跑VIO或LIO了，机载端压力小一些。（因为我机载端还要跑神经网络）这种方式的定位方案靠得住么？感觉肯定比LIO差一些，不知道具体差多少？
2. 增加T265后我需要更改下安装板机械结构，有个问题是T265的FOV是163度，这样就会拍到桨叶，桨叶是不断旋转的，是否会影响定位精度？当前D435应该也会拍到桨叶吧？
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

TheConquerK, 2024-05-14:
1.我个人建议还是用激光好一点，其实 跑LIO耗费的资源不会特别大。T265我们没有在真机上测试过，但是手头是有传感器的，个人感觉T265的直出Odom在小范围，光照良好且纹理特征明显的环境是可以用的，但是不是特别推荐，毕竟是比较早之前的产品了，国内现在有类似的产品比如VIOBOT这种可以试试，似乎精度是足够的，也带有一个微处理器可以做一些功能。
2.在现在这种安装情况下，D435/D435i并不会出现桨叶干扰的情况，如果安装T265出现问题的话可以适当修改感知模块上板来满足你的设计需求

Closed 2024-05-14.

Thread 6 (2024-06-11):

how to connect NUC pc to Kakute H7

NamDinhRobotics, 2024-06-11:
Dear team,

I want to express my gratitude for providing such an excellent resource. I have a question regarding the connection of the Kakute H7 to a NUC PC. Could you please provide guidance on the different methods of connection and how to configure parameters in QGroundControl?

If possible, could you provide instructions on this topic using the following link: [Kakute H7 product page](https://holybro.com/products/kakute-h7)?

Thank you in advance for your assistance.

Best regards,

TheConquerK, 2024-06-11:
Thank you for your recognition. In this project, NUC and Kakute mini H7 are connected via USB cable, using USB-A to USB-C wire. Parameters in QGroundControl are default.

NamDinhRobotics, 2024-06-12:
Great work, thanks for your answer.
The connection is shown as follows, and we don't need to connect through TELEM1.
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

After the connection, we don't need to change any parameters like EKF2 on PX4, and we can control the drone via Mavlink on the NUC. Is that correct?

Thanks so much for your help.
Bests,

TheConquerK, 2024-06-12:
The correct connection is shown in your picture. There's no need to connect telem1 in this project , unless you need a radio for QGC. We don't change EKF2 parameters in PX4 flight controller as it's all used in Stablized mode rather than Position or Altitude. The position controller is adpated in onboard computer.

NamDinhRobotics, 2024-06-13:
Great, thank you so much for your sharing,
Best wishes,

Closed 2024-06-11.

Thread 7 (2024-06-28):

只用雷达时候 不显示近处障碍物

zbcUN, 2024-06-28:
您好。我发现只用雷达的时候无法显示近处的障碍物 经常发生碰撞这是正常的吗？

TheConquerK, 2024-07-07:
这个问题可能与FAST-LIO中的雷达盲区配置有关，现有的雷达盲区配置为

TheConquerK, 2024-07-07:
src/realflight_modules/mid360_fastlio/src/FAST_LIO/config/mid360.yaml

TheConquerK, 2024-07-07:
这个问题可能与FAST-LIO中的雷达盲区配置有关，现有的雷达盲区配置为src/realflight_modules/mid360_fastlio/src/FAST_LIO/config/mid360.yaml line 11 blind参数，可以尝试把这个参数改小，并检查原始点云数据

Closed 2024-07-07.

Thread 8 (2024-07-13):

项目中Mid360驱动编译失败

comi-zhang, 2024-07-13:
ubuntu环境下，上位机已连接mid360,git下来该项目后进行catkin_make,雷达驱动部分报错
![Uploading Screenshot from 2024-07-12 13-21-30.png…]()

comi-zhang, 2024-07-13:
报错信息如下：
CMake Error at /opt/ros/noetic/share/catkin/cmake/catkin_workspace.cmake:121 (add_subdirectory):
  The source directory

    /home/uav/REAL_DRONE_400-main/src/realflight_modules/mid360_fastlio/src/livox_ros_driver/livox_ros_driver

  does not contain a CMakeLists.txt file.
Call Stack (most recent call first):
  CMakeLists.txt:69 (catkin_workspace)

-- +++ processing catkin package: 'fast_lio'
-- ==> add_subdirectory(realflight_modules/mid360_fastlio/src/FAST_LIO)
Current CPU archtecture: x86_64
Processer number:  16
core for MP: 3
-- Using these message generators: gencpp;geneus;genlisp;gennodejs;genpy
-- Could NOT find livox_ros_driver (missing: livox_ros_driver_DIR)
-- Could not find the required component 'livox_ros_driver'. The following CMake error indicates that you either need to install the package with the same name or change your environment so that it can be found.
CMake Error at /opt/ros/noetic/share/catkin/cmake/catkinConfig.cmake:83 (find_package):
  Could not find a package configuration file provided by "livox_ros_driver"
  with any of the following names:

    livox_ros_driverConfig.cmake
    livox_ros_driver-config.cmake

  Add the installation prefix of "livox_ros_driver" to CMAKE_PREFIX_PATH or
  set "livox_ros_driver_DIR" to a directory containing one of the above
  files.  If "livox_ros_driver" provides a separate development package or
  SDK, be sure it has been installed.
Call Stack (most recent call first):
  realflight_modules/mid360_fastlio/src/FAST_LIO/CMakeLists.txt:45 (find_package)

-- Configuring incomplete, errors occurred!
See also "/home/uav/REAL_DRONE_400-main/build/CMakeFiles/CMakeOutput.log".
See also "/home/uav/REAL_DRONE_400-main/build/CMakeFiles/CMakeError.log".
Invoking "cmake" failed

TheConquerK, 2024-07-13:
忽略报错，重复编译即可，catkin make还没编译到livox  ros driver

wjw112211, 2025-05-26:
您好，我也遇到了相同的问题，重复编译是报错后继续catkin_make吗？这样试了好多次还是报错，请问改怎么解决呢？

Closed 2024-07-13.

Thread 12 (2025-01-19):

起飞失败

unius589, 2025-01-19:
你好，咨询一下自动起飞失败的问题；我换了机架，轴距是400，自动起飞前VINS都没问题，里程计信息也正常；自动起飞脚本运行后电机加速旋转，但就是飞不起来，具体见视频；
因为考虑到安全问题，飞机外面增加了一个塑料的罩子，整机重量2.9kg，轴距400，7寸三叶桨；

目前做过以下尝试：
0. 已尝试增加hover_percentage的值，从0.3一路增加到0.6都飞不起来。

    已确认螺旋桨没有装反；
    电机用的KV值的 1100，力效表见图片。按照表格推算，0.55油门时，单个电机推力达到1kg多，总推力足以超过飞机重量啊；

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

<!-- Failed to upload "petal_20250119_111005.mp4" -->

unius589, 2025-01-19:
视频上传失败了，看这个链接吧 https://www.bilibili.com/video/BV1uuwqeJEgn/?spm_id_from=333.999.0.0

TheConquerK, 2025-01-19:
确认一下起飞时候的油门摇杆是否在中位

unius589, 2025-01-19:
遥控器在中位  减了一些重量  现在还剩2.5kg  和你教程中的比较接近了  请问您实际飞行的hover_percentage就是设置的0.35吗？ 谢谢

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

TheConquerK, 2025-01-19:
差不多，这个根据你们自己飞机在自稳模式下手飞悬停的油门来确定

Closed 2025-01-20.

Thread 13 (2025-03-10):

项目编译出错

Qi-Fei-7090, 2025-03-10:
作者您好！
最近在尝试复刻您的项目，我在git clone下来项目后尝试catkin_make编译，显示雷达驱动报错。
本人水平有限，希望作者能提供较为详细的解决方案或排查思路。感谢您的帮助！
终端返回完整信息如下：

`Base path: /home/uav/REAL_DRONE_400-main
Source space: /home/uav/REAL_DRONE_400-main/src
Build space: /home/uav/REAL_DRONE_400-main/build
Devel space: /home/uav/REAL_DRONE_400-main/devel
Install space: /home/uav/REAL_DRONE_400-main/install
####
#### Running command: "cmake /home/uav/REAL_DRONE_400-main/src -DCATKIN_DEVEL_PREFIX=/home/uav/REAL_DRONE_400-main/devel -DCMAKE_INSTALL_PREFIX=/home/uav/REAL_DRONE_400-main/install -G Unix Makefiles" in "/home/uav/REAL_DRONE_400-main/build"
####
-- Using CATKIN_DEVEL_PREFIX: /home/uav/REAL_DRONE_400-main/devel
-- Using CMAKE_PREFIX_PATH: /opt/ros/noetic
-- This workspace overlays: /opt/ros/noetic
-- Found PythonInterp: /usr/bin/python3 (found suitable version "3.8.10", minimum required is "3")
-- Using PYTHON_EXECUTABLE: /usr/bin/python3
-- Using Debian Python package layout
-- Using empy: /home/uav/.local/lib/python3.8/site-packages/em.py
-- Using CATKIN_ENABLE_TESTING: ON
-- Call enable_testing()
-- Using CATKIN_TEST_RESULTS_DIR: /home/uav/REAL_DRONE_400-main/build/test_results
-- Forcing gtest/gmock from source, though one was otherwise available.
-- Found gtest sources under '/usr/src/googletest': gtests will be built
-- Found gmock sources under '/usr/src/googletest': gmock will be built
-- Found PythonInterp: /usr/bin/python3 (found version "3.8.10")
-- Using Python nosetests: /usr/bin/nosetests3
-- catkin 0.8.10
-- BUILD_SHARED_LIBS is on
-- BUILD_SHARED_LIBS is on
-- ~~~~~~~~~~~~~~~~~~~~~~~~~~~~~~~~~~~~~~~~~~~~~~~~~
-- ~~  traversing 28 packages in topological order:
-- ~~  - catkin_simple
-- ~~  - realsense2_description
-- ~~  - decomp_ros_msgs
-- ~~  - cmake_utils
-- ~~  - map_generator
-- ~~  - plan_env
-- ~~  - path_searching
-- ~~  - pose_utils
-- ~~  - quadrotor_msgs
-- ~~  - poscmd_2_odom
-- ~~  - drone_detect
-- ~~  - odom_visualization
-- ~~  - livox_ros_driver
-- ~~  - livox_ros_driver2
-- ~~  - fast_lio
-- ~~  - local_sensing_node
-- ~~  - mockamap
-- ~~  - realsense2_camera
-- ~~  - so3_control
-- ~~  - traj_utils
-- ~~  - bspline_opt
-- ~~  - ego_planner
-- ~~  - rosmsg_tcp_bridge
-- ~~  - uav_utils
-- ~~  - px4ctrl
-- ~~  - so3_quadrotor_simulator
-- ~~  - decomp_ros_utils
-- ~~  - rviz_plugins
-- ~~~~~~~~~~~~~~~~~~~~~~~~~~~~~~~~~~~~~~~~~~~~~~~~~
-- +++ processing catkin package: 'catkin_simple'
-- ==> add_subdirectory(utils/catkin_simple)
-- +++ processing catkin package: 'realsense2_description'
-- ==> add_subdirectory(realflight_modules/realsense-ros/realsense2_description)
-- +++ processing catkin package: 'decomp_ros_msgs'
-- ==> add_subdirectory(utils/DecompROS/decomp_ros_msgs)
-- Using these message generators: gencpp;geneus;genlisp;gennodejs;genpy
-- decomp_ros_msgs: 4 messages, 0 services
-- +++ processing catkin package: 'cmake_utils'
-- ==> add_subdirectory(utils/cmake_utils)
-- +++ processing catkin package: 'map_generator'
-- ==> add_subdirectory(uav_simulator/map_generator)
-- Eigen found (include: /usr/include/eigen3, version: 3.3.7)
-- The imported target "vtkParseOGLExt" references the file
   "/usr/bin/vtkParseOGLExt-7.1"
but this file does not exist.  Possible reasons include:
* The file was deleted, renamed, or moved to another location.
* An install or uninstall procedure did not complete successfully.
* The installation package was faulty and contained
   "/usr/lib/cmake/vtk-7.1/VTKTargets.cmake"
but not all the files it references.

-- The imported target "vtkRenderingPythonTkWidgets" references the file
   "/usr/lib/x86_64-linux-gnu/libvtkRenderingPythonTkWidgets.so"
but this file does not exist.  Possible reasons include:
* The file was deleted, renamed, or moved to another location.
* An install or uninstall procedure did not complete successfully.
* The installation package was faulty and contained
   "/usr/lib/cmake/vtk-7.1/VTKTargets.cmake"
but not all the files it references.

-- The imported target "vtk" references the file
   "/usr/bin/vtk"
but this file does not exist.  Possible reasons include:
* The file was deleted, renamed, or moved to another location.
* An install or uninstall procedure did not complete successfully.
* The installation package was faulty and contained
   "/usr/lib/cmake/vtk-7.1/VTKTargets.cmake"
but not all the files it references.

-- The imported target "pvtk" references the file
   "/usr/bin/pvtk"
but this file does not exist.  Possible reasons include:
* The file was deleted, renamed, or moved to another location.
* An install or uninstall procedure did not complete successfully.
* The installation package was faulty and contained
   "/usr/lib/cmake/vtk-7.1/VTKTargets.cmake"
but not all the files it references.

-- OpenNI found (include: /usr/include/ni, lib: /usr/lib/libOpenNI.so)
-- OpenNI2 found (include: /usr/include/openni2, lib: /usr/lib/libOpenNI2.so)
** WARNING ** io features related to pcap will be disabled
** WARNING ** io features related to png will be disabled
** WARNING ** io features related to libusb-1.0 will be disabled
-- OpenNI found (include: /usr/include/ni, lib: /usr/lib/libOpenNI.so)
-- OpenNI2 found (include: /usr/include/openni2, lib: /usr/lib/libOpenNI2.so)
-- QHULL found (include: /usr/include, lib: optimized;/usr/lib/x86_64-linux-gnu/libqhull.so;debug;/usr/lib/x86_64-linux-gnu/libqhull.so)
-- OpenNI found (include: /usr/include/ni, lib: /usr/lib/libOpenNI.so)
-- looking for PCL_COMMON
-- looking for PCL_KDTREE
-- looking for PCL_OCTREE
-- looking for PCL_SEARCH
-- looking for PCL_SAMPLE_CONSENSUS
-- looking for PCL_FILTERS
-- looking for PCL_2D
-- looking for PCL_GEOMETRY
-- looking for PCL_IO
-- looking for PCL_FEATURES
-- looking for PCL_ML
-- looking for PCL_SEGMENTATION
-- looking for PCL_VISUALIZATION
-- looking for PCL_SURFACE
-- looking for PCL_REGISTRATION
-- looking for PCL_KEYPOINTS
-- looking for PCL_TRACKING
-- looking for PCL_RECOGNITION
-- looking for PCL_STEREO
-- looking for PCL_APPS
-- looking for PCL_IN_HAND_SCANNER
-- looking for PCL_POINT_CLOUD_EDITOR
-- looking for PCL_OUTOFCORE
-- looking for PCL_PEOPLE
-- +++ processing catkin package: 'plan_env'
-- ==> add_subdirectory(planner/plan_env)
-- Eigen found (include: /usr/include/eigen3, version: 3.3.7)
-- The imported target "vtkParseOGLExt" references the file
   "/usr/bin/vtkParseOGLExt-7.1"
but this file does not exist.  Possible reasons include:
* The file was deleted, renamed, or moved to another location.
* An install or uninstall procedure did not complete successfully.
* The installation package was faulty and contained
   "/usr/lib/cmake/vtk-7.1/VTKTargets.cmake"
but not all the files it references.

-- The imported target "vtkRenderingPythonTkWidgets" references the file
   "/usr/lib/x86_64-linux-gnu/libvtkRenderingPythonTkWidgets.so"
but this file does not exist.  Possible reasons include:
* The file was deleted, renamed, or moved to another location.
* An install or uninstall procedure did not complete successfully.
* The installation package was faulty and contained
   "/usr/lib/cmake/vtk-7.1/VTKTargets.cmake"
but not all the files it references.

-- The imported target "vtk" references the file
   "/usr/bin/vtk"
but this file does not exist.  Possible reasons include:
* The file was deleted, renamed, or moved to another location.
* An install or uninstall procedure did not complete successfully.
* The installation package was faulty and contained
   "/usr/lib/cmake/vtk-7.1/VTKTargets.cmake"
but not all the files it references.

-- The imported target "pvtk" references the file
   "/usr/bin/pvtk"
but this file does not exist.  Possible reasons include:
* The file was deleted, renamed, or moved to another location.
* An install or uninstall procedure did not complete successfully.
* The installation package was faulty and contained
   "/usr/lib/cmake/vtk-7.1/VTKTargets.cmake"
but not all the files it references.

-- OpenNI found (include: /usr/include/ni, lib: /usr/lib/libOpenNI.so)
-- OpenNI2 found (include: /usr/include/openni2, lib: /usr/lib/libOpenNI2.so)
** WARNING ** io features related to pcap will be disabled
** WARNING ** io features related to png will be disabled
** WARNING ** io features related to libusb-1.0 will be disabled
-- OpenNI found (include: /usr/include/ni, lib: /usr/lib/libOpenNI.so)
-- OpenNI2 found (include: /usr/include/openni2, lib: /usr/lib/libOpenNI2.so)
-- QHULL found (include: /usr/include, lib: optimized;/usr/lib/x86_64-linux-gnu/libqhull.so;debug;/usr/lib/x86_64-linux-gnu/libqhull.so)
-- OpenNI found (include: /usr/include/ni, lib: /usr/lib/libOpenNI.so)
-- looking for PCL_COMMON
-- looking for PCL_KDTREE
-- looking for PCL_OCTREE
-- looking for PCL_SEARCH
-- looking for PCL_SAMPLE_CONSENSUS
-- looking for PCL_FILTERS
-- looking for PCL_2D
-- looking for PCL_GEOMETRY
-- looking for PCL_IO
-- looking for PCL_FEATURES
-- looking for PCL_ML
-- looking for PCL_SEGMENTATION
-- looking for PCL_VISUALIZATION
-- looking for PCL_SURFACE
-- looking for PCL_REGISTRATION
-- looking for PCL_KEYPOINTS
-- looking for PCL_TRACKING
-- looking for PCL_RECOGNITION
-- looking for PCL_STEREO
-- looking for PCL_APPS
-- looking for PCL_IN_HAND_SCANNER
-- looking for PCL_POINT_CLOUD_EDITOR
-- looking for PCL_OUTOFCORE
-- looking for PCL_PEOPLE
-- Found PCL: pcl_common;pcl_kdtree;pcl_octree;pcl_search;pcl_sample_consensus;pcl_filters;pcl_io;pcl_features;pcl_ml;pcl_segmentation;pcl_visualization;pcl_surface;pcl_registration;pcl_keypoints;pcl_tracking;pcl_recognition;pcl_stereo;pcl_apps;pcl_outofcore;pcl_people;/usr/lib/x86_64-linux-gnu/libboost_system.so;/usr/lib/x86_64-linux-gnu/libboost_filesystem.so;/usr/lib/x86_64-linux-gnu/libboost_date_time.so;/usr/lib/x86_64-linux-gnu/libboost_iostreams.so;/usr/lib/x86_64-linux-gnu/libboost_regex.so;optimized;/usr/lib/x86_64-linux-gnu/libqhull.so;debug;/usr/lib/x86_64-linux-gnu/libqhull.so;/usr/lib/libOpenNI.so;/usr/lib/libOpenNI2.so;vtkChartsCore;vtkCommonColor;vtkCommonCore;vtksys;vtkCommonDataModel;vtkCommonMath;vtkCommonMisc;vtkCommonSystem;vtkCommonTransforms;vtkCommonExecutionModel;vtkFiltersGeneral;vtkCommonComputationalGeometry;vtkFiltersCore;vtkInfovisCore;vtkFiltersExtraction;vtkFiltersStatistics;vtkImagingFourier;vtkImagingCore;vtkalglib;vtkRenderingContext2D;vtkRenderingCore;vtkFiltersGeometry;vtkFiltersSources;vtkRenderingFreeType;/usr/lib/x86_64-linux-gnu/libfreetype.so;/usr/lib/x86_64-linux-gnu/libz.so;vtkFiltersModeling;vtkImagingSources;vtkInteractionStyle;vtkInteractionWidgets;vtkFiltersHybrid;vtkImagingColor;vtkImagingGeneral;vtkImagingHybrid;vtkIOImage;vtkDICOMParser;vtkmetaio;/usr/lib/x86_64-linux-gnu/libjpeg.so;/usr/lib/x86_64-linux-gnu/libpng.so;/usr/lib/x86_64-linux-gnu/libtiff.so;vtkRenderingAnnotation;vtkRenderingVolume;vtkIOXML;vtkIOCore;vtkIOXMLParser;/usr/lib/x86_64-linux-gnu/libexpat.so;vtkIOGeometry;vtkIOLegacy;vtkIOPLY;vtkRenderingLOD;vtkViewsContext2D;vtkViewsCore;vtkRenderingContextOpenGL2;vtkRenderingOpenGL2;FLANN::FLANN (Required is at least version "1.7")
-- +++ processing catkin package: 'path_searching'
-- ==> add_subdirectory(planner/path_searching)
-- Eigen found (include: /usr/include/eigen3, version: 3.3.7)
-- The imported target "vtkParseOGLExt" references the file
   "/usr/bin/vtkParseOGLExt-7.1"
but this file does not exist.  Possible reasons include:
* The file was deleted, renamed, or moved to another location.
* An install or uninstall procedure did not complete successfully.
* The installation package was faulty and contained
   "/usr/lib/cmake/vtk-7.1/VTKTargets.cmake"
but not all the files it references.
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

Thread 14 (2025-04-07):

使用px4ctrl自动起飞无人机首先飞到指定高度，之后向天上猛冲

XXLiu-HNU, 2025-04-07:
作者你好，感谢开源如此优秀的项目，对于小白来说十分友好。我们实验室也进行了该项目的复现。

但是最近我们在测试的时候，发现无人机有时候会在**自动起飞之后直接往天上猛冲**得情况。
### 下边是我们的一下背景:
## 硬件:

**飞控** ：NxtPx4 v2
**雷达**：MID360
**动力套件**：250mm机架，Tmotor F60pro KV1750，实测手摇情况良好，起飞油门大概在0.4左右。

## 软件:
**定位算法**：使用该项目修改后的Fast-LIO，实际测试时绕场地行走定位效果良好；
**控制算法**：控制算法为该项目中的px4ctrl，对应的修改了悬停油门和话题映射关系；

## 测试流程：
1. 启动mavros、fastlio
2. 遥控器档位拨好
3. 运行px4ctrl
4. 发布起飞话题

## 实际测试视频：
可以看到无人机在起飞到0.5m之后突然加速向上飞，后续检查录包文件发现定位也没有飘
https://github.com/user-attachments/assets/a9d6d0cf-c343-447c-854d-d122ec578e24

## 尝试解决方法

最开始以为是油门反向的问题，所以仔细检查油门之后，并在set_hov_with_rc里边对高度进行了限制：
```
void PX4CtrlFSM::set_hov_with_rc()
{
	ros::Time now = ros::Time::now();
	double delta_t = (now - last_set_hover_pose_time).toSec();
	last_set_hover_pose_time = now;

	hover_pose(0) += rc_data.ch[1] * param.max_manual_vel * delta_t * (param.rc_reverse.pitch ? 1 : -1);
	hover_pose(1) += rc_data.ch[0] * param.max_manual_vel * delta_t * (param.rc_reverse.roll ? 1 : -1);
	hover_pose(2) += rc_data.ch[2] * param.max_manual_vel * delta_t * (param.rc_reverse.throttle ? 1 : -1);
	hover_pose(3) += rc_data.ch[3] * param.max_manual_vel * delta_t * (param.rc_reverse.yaw ? 1 : -1);

	if (hover_pose(2) < -0.3)
		hover_pose(2) = -0.3;
        // 这里增加了高度限制
        if (hover_pose(2) > 1.5)
		hover_pose(2) = 1.5;
}
```
但是测试还是会存在这个问题，因此想咨询一下大佬看看有没有什么建议，感激不尽！！

TheConquerK, 2025-04-08:
感谢对项目的支持。
这种情况看起来非常的不对劲
如果可以的话检查一下
1.遥控器油门通道是否处于中位
2.定位是否出现发散情况
3.检查一下输出给mavros的推力
正常情况应该能够在目标悬停高度完成稳定悬停

TheConquerK, 2025-04-08:
是可以的，个人认为在雷达平装的情况下差别不大。如果雷达倾斜安装，建议使用飞控IMU作为输入

Coder0551, 2025-05-15:
@XXLiu-HNU 您好，请问问题解决了吗？期待回复，谢谢！

XXLiu-HNU, 2025-05-15:
更新一下，后边我们还是没用px4ctrl，因为没有找到具体的BUG，飞机也摔坏了好几次！不过借鉴px4ctrl自己写了一个[控制器](https://github.com/HNU-CAT/pid_ctrl)，现在飞的稳稳的！

[测试效果](https://github.com/user-attachments/assets/28321dd7-60d3-4f61-940d-227ff98c5790)

Closed 2025-05-06.

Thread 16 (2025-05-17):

飞机自动起飞后缓慢上升

Coder0551, 2025-05-17:
作者您好！感谢你们的开源分享，我们已经基本上复现了项目。目前的问题是：飞机自动起飞之后，飞机会缓慢继续往天上飞。从RVIZ上看不到漂移的迹象。期待回复，谢谢！

Coder0551, 2025-05-18:
> 作者您好！感谢你们的开源分享，我们已经基本上复现了项目。目前的问题是：飞机自动起飞之后，飞机会缓慢继续往天上飞。从RVIZ上看不到漂移的迹象。期待回复，谢谢！

已解决，原因是起飞前遥控器油门不在50%的位置

Closed 2025-05-28.

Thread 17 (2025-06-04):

使用flight_type=2模式飞行waypoints不能进入状态机

wjw112211, 2025-06-04:
您好，我们使用下面这种模式飞行的时候：
<arg name="flight_type" value="2" />

<arg name="point_num" value="1" />
        <arg name="point0_x" value="15" />
        <arg name="point0_y" value="0" />
        <arg name="point0_z" value="1" />
        <arg name="point1_x" value="0.0" />
        <arg name="point1_y" value="0.0" />
        <arg name="point1_z" value="1.0" />
        <arg name="point2_x" value="15.0" />
        <arg name="point2_y" value="0.0" />
        <arg name="point2_z" value="1.0" />
        <arg name="point3_x" value="0.0" />
        <arg name="point3_y" value="0.0" />
        <arg name="point3_z" value="1.0" />
        <arg name="point4_x" value="15.0" />
        <arg name="point4_y" value="0.0" />
        <arg name="point4_z" value="1.0" />
出现问题，xml配置文件根据相应waypoints的个数修改了。
切换遥控器切换状态后，运行px4ctrl runctrl，再运行single_run_in_exp.launch和自动起飞后，

px4ctrlfsm打印：
AUTO_TAKEOFFF->AUTO_HOVER.

然后ego_replan_fsm打印:
[FSM]:state:WAIT_TARGET
wait for goal or trigger.

飞机大概处于悬停状态10S后，就突然往天上蹿。请问下这个怎么解决？

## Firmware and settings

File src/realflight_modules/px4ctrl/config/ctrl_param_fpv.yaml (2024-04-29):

#########################################################################
# ⭐⭐⭐  Set parameters carefully for satisfied performance!   ⭐⭐⭐ #
#########################################################################

mass        : 2.67 # kg 
gra         : 9.81 
pose_solver : 1     # 0:From ZhepeiWang (drag & less singular) 1:From ZhepeiWang, 2:From rotor-drag    
ctrl_freq_max   : 100.0
use_bodyrate_ctrl: false
max_manual_vel: 1.0
max_angle: 30  # Attitude angle limit in degree. A negative value means no limit.
low_voltage: 13.2 # 4S battery

rc_reverse: # *
    roll: false
    pitch: false
    yaw: false
    throttle: false

auto_takeoff_land:
    enable: true
    enable_auto_arm: true
    no_RC: false
    takeoff_height: 0.5 # m
    takeoff_land_speed: 0.3 # m/s

thrust_model: # The model that maps thrust signal u(0~1) to real thrust force F(Unit:N): F=K1*Voltage^K2*(K3*u^2+(1-K3)*u). 
    print_value: false # display the value of “thr_scale_compensate” or “hover_percentage” during thrust model estimating.
    accurate_thrust_model: false  # This can always enabled if don't require accurate control performance :-)
    # accurate thrust mapping parameters
    K1: 0.7583 # Needs precise calibration!
    K2: 1.6942 # Needs precise calibration!
    K3: 0.6786 # Needs precise calibration! K3 equals THR_MDL_FAC in https://docs.px4.io/master/en/config_mc/pid_tuning_guide_multicopter.html.
    # approximate thrust mapping parameters
    hover_percentage: 0.35  # Thrust percentage in Stabilize/Arco mode # *

gain: 
    # Cascade PID controller. Recommend to read the code.
    Kp0: 2.0
    Kp1: 2.0 
    Kp2: 2.0
    Kv0: 1.5
    Kv1: 1.5
    Kv2: 1.5
    # ↓↓↓ No use now --
    Kvi0: 0.0
    Kvi1: 0.0
    Kvi2: 0.0
    Kvd0: 0.0
    Kvd1: 0.0
    Kvd2: 0.0
    # ↓↓↓ Only used in rate control mode.
    KAngR: 20.0
    KAngP: 20.0
    KAngY: 20.0

rotor_drag:  
    x: 0.0  # The reduced acceleration on each axis caused by rotor drag. Unit:(m*s^-2)/(m*s^-1).
    y: 0.0  # Same as above
    z: 0.0  # Same as above
    k_thrust_horz: 0.0 # Set to 0 recommended... --

msg_timeout:
    odom: 0.5
    rc:   0.5
    cmd:  0.5
    imu:  0.5
    bat:  0.5

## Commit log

2024-04-29 20240429 Project_Update
    update Readme.md
    [25mm铝柱-分电板.STEP, 50mm铝柱-电池仓.STEP, F100-m2810.STEP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]
2024-04-29 20240429 update & upload
    完结撒花
    [purchase_list.xlsx]
2025-11-17 Derivative Design update
    [R7040_GD_0525_001_Result_001.step]
